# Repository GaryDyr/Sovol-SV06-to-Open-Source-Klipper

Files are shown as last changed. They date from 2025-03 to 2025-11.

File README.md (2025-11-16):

The file, sv06_to_klipper.pdf, is a running tutorial history of changing a stock Sovol SV06 printer from Marlin to open source Klipper. It describes the process, trial and trbulations of the changeover, and calibrations needed.

The file,  klipper_bed_leveling_experiments.pdf, lays out the problems of trying to achieve a level bed with the standard inductive probe of the SV06. It deals with issues where the inductive probe cannot faithfully resolve the bed surface. Potential reasons for the lack of correlation are discussed. 
The Bed_Calc.xlsm file is an Excel file that is associated with the bed leveling experiments. It contains calculation methods related to adjusting the Z tilt, and how the klipper bed mesh calibration data was manually altered to achieve good first layer prints.

The 3x3 first layer print used for first layer uniformity is included. 

A new calibration "tree" model files that are used to calibrate the x and y stepper motor settings is also included.

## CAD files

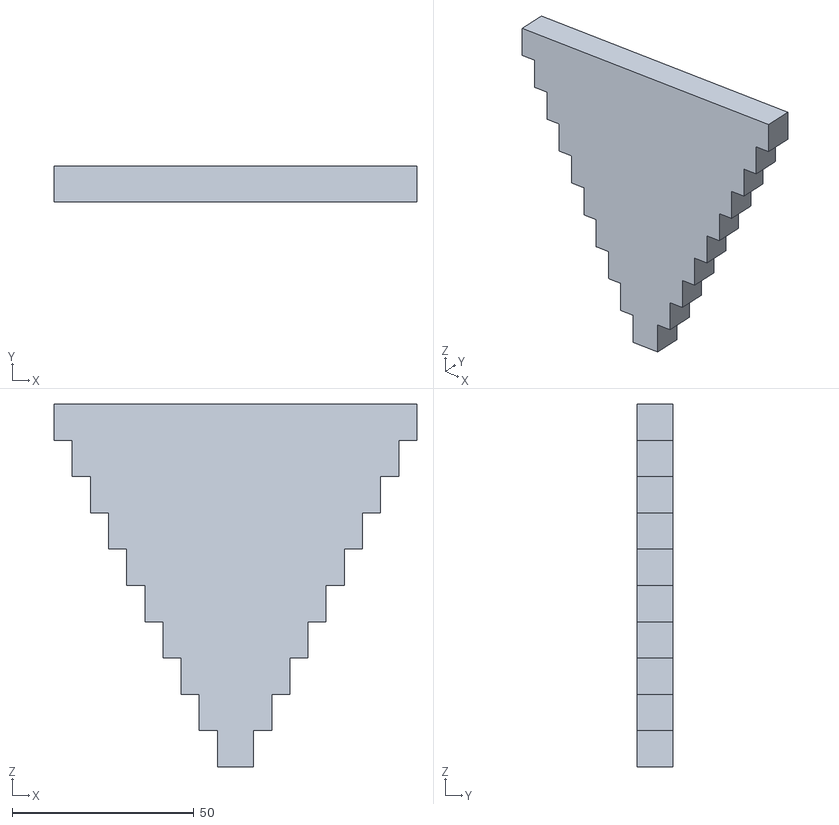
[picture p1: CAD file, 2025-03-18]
XY Step Pyramid v1.stl
100.0 x 10.0 x 100.0

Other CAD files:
XY Step Pyramid v1.f3d

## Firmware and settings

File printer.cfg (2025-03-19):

# This file contains pin mappings for the stock Sovol SV06
# To use this config, during "make menuconfig" select the
# STM32F103 with a "28KiB bootloader" and serial (on USART1 PA10/PA9) communication.
# Also, since it is using the GD32F103, please select Disable SWD at startup
#
# Flash this firmware by copying "out/klipper.bin" to a SD card and
# turning on the printer with the card inserted. The firmware
# filename must end in ".bin" and must not match the last filename
# that was flashed.
# grd-this file has been modified based on some of the values found in the Sovol SV06 klipper printer.cfg file
#
# See docs/Config_Reference.md for a description of parameters.
# Data here has been updated somewhat based on the cfg file for Sovol's Klipper Screen

[include mainsail.cfg]

#some of these may conflict with other macros buried here or in other cfg files, particularly misc-macros; start without them.
#[include ./cfg/misc-macros.cfg]
#[include ./cfg/PARKING.cfg]
#[include ./cfg/MECANICAL_GANTRY_CALIBRATION.cfg]

[include ./cfg/Z_Tramming.cfg]
[include ./cfg/TEST_SPEED.cfg]
#[include ./cfg/adxl-direct.cfg]

[mcu]
#serial:/dev/serial/by-id/usb-1a86_USB2.0-Serial-if00-port0
#bottom back USB port id was used.
serial: /dev/serial/by-id/usb-1a86_USB_Serial-if00-port0
restart_method: command

[virtual_sdcard]
#/home/biqu/printer_data
#mainsail.cfg has below format
#~/home/printer_data/gcodes

[save_variables]
filename =/home/biqu/printer_data/config/saved_variables.cfg

[printer]
kinematics: cartesian
max_velocity: 600 
max_accel: 10000 ;8000
max_z_velocity: 15
max_z_accel: 150
square_corner_velocity: 3.0

[stepper_x]
step_pin: PC2
dir_pin: !PB9
enable_pin: !PC3
microsteps: 16
rotation_distance: 40
endstop_pin: tmc2209_stepper_x:virtual_endstop
position_endstop: 0
position_max: 225
homing_speed: 50 ;70
homing_retract_dist: 0
step_pulse_duration:0.000002

[tmc2209 stepper_x]
uart_pin: PC1
run_current: 0.860
stealthchop_threshold: 0
interpolate: False
sense_resistor: 0.150
uart_address: 3
driver_SGTHRS: 110 ;89
diag_pin: PA5

[stepper_y]
step_pin: PB8
dir_pin: PB7
enable_pin: !PC3
microsteps: 16
rotation_distance: 40
endstop_pin: tmc2209_stepper_y:virtual_endstop
position_endstop: 0
position_max: 225
homing_speed: 60
homing_retract_dist: 0

[tmc2209 stepper_y]
uart_pin: PC0
run_current: 0.900
stealthchop_threshold: 0
interpolate: False
sense_resistor: 0.150
uart_address: 3
driver_SGTHRS: 88
diag_pin: PA6

[stepper_z]
step_pin: PB6
dir_pin: !PB5
enable_pin: !PC3
microsteps: 16
rotation_distance: 4
endstop_pin: probe:z_virtual_endstop
position_min: -4
position_max: 261
homing_speed: 6

[tmc2209 stepper_z]
uart_pin: PA15
run_current: 1.000
stealthchop_threshold: 0
interpolate: False
sense_resistor: 0.150
uart_address: 3
diag_pin: PA7

[extruder]
max_extrude_only_distance: 100.0
step_pin: PB4
dir_pin: !PB3
enable_pin: !PC3
microsteps: 16
rotation_distance: 4.56
nozzle_diameter: 0.400
filament_diameter: 1.750
heater_pin: PA1
sensor_type: EPCOS 100K B57560G104F
sensor_pin: PC5
#control: pid
#pid_kd: 86.991
#pid_kp: 21.479
#pid_ki: 1.326
min_temp: 0
max_temp: 300
pressure_advance: 0.12 ;PLA

[tmc2209 extruder]
uart_pin: PC14
run_current: 0.550
stealthchop_threshold: 0
interpolate: False
sense_resistor: 0.150
uart_address: 3

[heater_bed]
heater_pin: PA2
sensor_type: EPCOS 100K B57560G104F
sensor_pin: PC4
#control: pid
#pid_kp: 64.440
#pid_ki: 0.773
#pid_kd: 1343.571
min_temp: 0
max_temp: 130

[fan]
pin: PA0

[probe]
pin: PB1
x_offset: 27
y_offset: -20
#z_offset: 0
samples: 3
samples_tolerance: 0.015
samples_tolerance_retries: 5

[safe_z_home]
home_xy_position: 85,135
z_hop: 10
z_hop_speed: 5

[bed_mesh]
speed: 120
horizontal_move_z: 5
mesh_min: 27, 12
mesh_max: 210, 205
probe_count: 10,10
algorithm: bicubic
bicubic_tension: 0.5
fade_start: 2
fade_end: 10
mesh_pps:4,4
move_check_distance: 3
#fade_target: 0

[display]
lcd_type: st7920
cs_pin: PB12
sclk_pin: PB13
sid_pin: PB15
encoder_pins: ^PB14, ^PB10
click_pin: ^!PB2

[respond]
default_type: echo
#   Sets the default prefix of the "M118" and "RESPOND" output to one
#   of the following:
#       echo: "echo: " (This is the default)
#       command: "// "
#       error: "error!"
#default_prefix: echo:
#   Directly sets the default prefix. If present, this value will
#   override the "default_type".

[auto_speed]
max_missed: 20

#[axis_twist_compensation]
#speed: 50
#horizontal_move_z: 5
#calibrate_start_x: 27
#calibrate_end_x: 193
#calibrate_y: 110
#calibrate_start_y: 20
#calibrate_end_y: 200
#calibrate_x: 110

[gcode_macro START_PRINT]
gcode:
    # Parameters
    {% set bedtemp = params.BED|default(60)|int %}
    {% set extrudertemp = params.HOTEND|default(195)|int %}
    RESPOND TYPE=echo MSG="START_PRINT CALLED"
    # set and wait for bet T
    M190 S{bedtemp}
    #set and wait for extruder T
    M109 S{extrudertemp} 
    M84 E ; Disable E Motor for probe accuracy on direct drive systems
    G90 ; Absolute positioning
    G92 E0 ; Reset Extruder distance to 0
    G1 E-1 ; Retracts filament to prevent blobs during probing
    G92 E0 ; Reset Extruder distance to 0
    G28 ; home all axes
    BED_MESH_PROFILE LOAD="default" ; Loads the mesh
    G92 E0     ; reset extruder
    G1 Z1.0 F3000    ; move z up little to prevent scratching of surface
    G1 X0.1 Y20 Z0.3 F5000.0  ; move to start-line position
    G1 X0.1 Y200.0 Z0.3 F1500.0 E15  ; draw 1st line
    G1 X0.4 Y200.0 Z0.3 F5000.0  ; move to side a little
    G1 X0.4 Y20 Z0.3 F1500.0 E30  ; draw 2nd line
    G92 E0     ; reset extruder
    G1 Z2.0 F3000    ; move z up little to prevent scratching of surface
 
[gcode_macro END_PRINT]
gcode:
    G91 ;Relative positionning
    G1 E-2 F500 ;Retract a bit
    G1 E-2 Z0.2 F200 ;Retract and raise Z
    G1 X5 Y5 F3000 ;Wipe out
    G1 Z10 ;Raise Z more
    M106 S0 ;Turn-off fan
    M104 S0 ;Turn-off hotend
    M140 S0 ;Turn-off bed
    G90 ;Absolute positionning
    G1 X10 Y210 ;Present print
    M84 X Y E ;Disable all steppers but Z
    RESPOND TYPE=echo MSG="Print Finished!"

[input_shaper]
#shaper_freq_x: 0
#shaper_type_x: mzv
#shaper_freq_y: 0
#shaper_type_y: mzv

#can use this or the macro in /cfg/ ;basically the same
#[mcu CB1]
#serial: /tmp/klipper_host_mcu

#[adxl345]
#cs_pin: CB1: None
#spi_bus: spidev1.1
#axes_map: z,y,-x # Modify according to the actual orientation of the ADXL345 installed on the printer.

#[resonance_tester]
#accel_chip: adxl345
#probe_points:
#	100, 100, 20 #and example

#*# <---------------------- SAVE_CONFIG ---------------------->
#*# DO NOT EDIT THIS BLOCK OR BELOW. The contents are auto-generated.
#*#
#*# [heater_bed]
#*# control = pid
#*# pid_kp = 68.574
#*# pid_ki = 1.398
#*# pid_kd = 840.888
#*#
#*# [extruder]
#*# control = pid
#*# pid_kp = 27.259
#*# pid_ki = 2.300
#*# pid_kd = 80.755
#*#
#*# [probe]
#*# z_offset = 1.560
#*#
#*# [input_shaper]
#*# shaper_type_x = zv
#*# shaper_freq_x = 55.6
#*# shaper_type_y = 2hump_ei
#*# shaper_freq_y = 61.4
#*#
#*# [bed_mesh default]
#*# version = 1
#*# points =
#*#        0.009583,  -0.074167,  -0.126667,  -0.110000,   -0.119583,  -0.108750,  -0.127083,  -0.121250,  -0.102763, -0.121811
#*#        -0.003541,  -0.062083,  -0.100000,  -0.086250,   -0.094167,  -0.093750,  -0.104167,  -0.090833,  -0.091197, -0.120328
#*#        0.000833,  0.002500,  -0.045833,  -0.044167,   -0.066250,  -0.063333,  -0.085417,  -0.072917,  -0.082965, -0.100429
#*#        0.009583,  -0.000417,  -0.027917,  -0.017917,   -0.045417,  -0.045417,  -0.070000,  -0.059583,  -0.058069, -0.086033
#*#        0.025833,  0.020833,  -0.005000,  -0.000833,   -0.036667,  -0.041250,  -0.071667,  -0.062083,  -0.068342, -0.121807
#*#        0.034583,  0.020417,  -0.007500,  -0.006667,   -0.050833,  -0.053333,  -0.072500,  -0.066667,  -0.073722, -0.124635
#*#        0.028750,  0.021667,  -0.011667,  -0.006667,   -0.042500,  -0.046250,  -0.072917,  -0.074167,  -0.084936, -0.127566
#*#        0.023750,  -0.017500,  -0.032500,  -0.015417,   -0.052083,  -0.052500,  -0.086250,  -0.085833,  -0.121982, -0.141337
#*#        -0.070127,  -0.067500,  -0.068750,  -0.040417,   -0.067500,  -0.067083,  -0.093333,  -0.098750,  -0.154866, -0.161247
#*#        -0.082590,  -0.050417,  -0.050000,  -0.017500,   -0.067083,  -0.070000,  -0.095000,  -0.107500,  -0.153996, -0.159667
#*# x_count = 10
#*# y_count = 10
#*# mesh_x_pps = 4
#*# mesh_y_pps = 4
#*# algo = bicubic
#*# tension = 0.5
#*# min_x = 27.0
#*# max_x = 209.96999999999997
#*# min_y = 12.0
#*# max_y = 204.95999999999998

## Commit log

2025-03-18 03-18-2024 initial upload
    [Bed_Calc.xlsm, XY Step Pyramid v1.f3d, XY Step Pyramid v1.stl]
2025-03-19 Added printer.cfg file as example
    [printer.cfg]
2025-03-19 Update README.md
    Added info on printer.cfg file.
